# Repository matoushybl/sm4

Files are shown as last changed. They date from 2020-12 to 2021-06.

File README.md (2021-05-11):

# SM4 Stepper motor controller

This repository contains everything related to the SM4 Stepper motor controller project.

The project structure is as follows:
```
.github/ ... workflows for CI, releases, etc.
Hardware/ ... everything related to hardware - KiCAD projects, DS, etc.
Poster/ ... source file for a future poster
Software/ ... the controller and embedded firmware
Thesis/ ... the TeX source code for my Master's Thesis
```

## Authors
* Matous Hybl

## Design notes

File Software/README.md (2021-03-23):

# Software

## Known issues

* the main loop cannot run @ 1 kHz as the readings of the encoder timer are zero, this is likely a software bug. The current workaround is to lower the control frequency to 100 Hz.

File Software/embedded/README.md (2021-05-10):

# `SM4-firmware`

> A firmware for the SM4 dual channel stepper motor controller.

## TODO
 - [ ] Test CANOpen
 - [ ] Implement USB
 - [ ] Implement I2C
 - [ ] Improve architecture and module structure

## Dependencies

#### 1. `flip-link`:

```console
$ cargo install flip-link
```

#### 2. `probe-run`:

``` console
$ cargo install probe-run
```

## Setup

## Support

TODO: Add affiliation with university, rust-embedded, etc

The firmware is based on tooling from the [Knurling] project, [Ferrous Systems]' effort at
improving tooling used to develop for embedded systems.

## License

Licensed under MIT license ([LICENSE-MIT](../LICENSE-MIT) or http://opensource.org/licenses/MIT).

[Knurling]: https://knurling.ferrous-systems.com
[Ferrous Systems]: https://ferrous-systems.com/
[GitHub Sponsors]: https://github.com/sponsors/knurling-rs

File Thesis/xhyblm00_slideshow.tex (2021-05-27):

% Soubory musí být v kódování, které je nastaveno v příkazu \usepackage[...]{inputenc}
% (tento soubor je sdílený s textem práce)

\documentclass[%        Základní nastavení
  %draft,    				  % Testovací překlad
  12pt,       				% Velikost základního písma je 12 bodů
	t,                  % obsah slajdů bude vždy začínat od shora (nebude vertikálně centrovaný)
	aspectratio=1610,   % poměr stran bude 16:10 (všechny projektory v učebnách na Technické 12 Brno),
	                    % další volby jsou 43, 149, 169, 54, 32.
	unicode,						% Záložky a informace budou v kódování unicode
]{beamer}				    	% Dokument třídy 'zpráva', vhodná pro sazbu závěrečných prací s kapitolami
%\usepackage{etex}

\usepackage[utf8]		  % Kódování zdrojových souborů je v UTF-8
	{inputenc}					% Balíček pro nastavení kódování zdrojových souborů
	
\usepackage{graphicx} % Balíček 'graphicx' pro vkládání obrázků
											% Nutné pro vložení logotypů školy a fakulty

\usepackage[          % Balíček 'acronym' pro sazby zkratek a symbolů
	nohyperlinks				% Nebudou tvořeny hypertextové odkazy do seznamu zkratek
]{acronym}						
											% Nutné pro použití prostředí 'acronym' balíčku 'thesis'

%% Balíček hyperref je volán třídou beamer automaticky, proto není třeba následujícího kódu:
%\usepackage[
%	breaklinks=true,		% Hypertextové odkazy mohou obsahovat zalomení řádku
%	hypertexnames=false % Názvy hypertextových odkazů budou tvořeny
%											% nezávisle na názvech TeXu
%]{hyperref}						% Balíček 'hyperref' pro sazbu hypertextových odkazů
%											% Nutné pro použití příkazu 'nastavenipdf' balíčku 'thesis'

\usepackage{cmap} 		% Balíček cmap zajišťuje, že PDF vytvořené `pdflatexem' je
											% plně "prohledávatelné" a "kopírovatelné"

%\usepackage{upgreek}	% Balíček pro sazbu stojatých řeckých písmem
											%% např. stojaté pí: \uppi
											%% např. stojaté mí: \upmu (použitelné třeba v mikrometrech)
											%% pozor, grafická nekompatibilita s fonty typu Computer Modern!

%\usepackage{amsmath} %balíček pro sabu náročnější matematiky

\usepackage{booktabs} % Balíček, který umožňuje v tabulce používat
                      % příkazy \toprule, \midrule, \bottomrule

%%%%%%%%%%%%%%%%%%%%%%%%%%%%%%%%%%%%%%%%%%%%%%%%%%%%%%%%%%%%%%%%%
%%%%%%      Definice informací o dokumentu             %%%%%%%%%%
%%%%%%%%%%%%%%%%%%%%%%%%%%%%%%%%%%%%%%%%%%%%%%%%%%%%%%%%%%%%%%%%%

\input{nastaveni}      % v tomto souboru doplňte údaje o sobě, o názvu práce...

%%%%%%%%%%%%%%%%%%%%%%%%%%%%%%%%%%%%%%%%%%%%%%%%%%%%%%%%%%%%%%%%%%%%%%%%

%%%%%%%%%%%%%%%%%%%%%%%%%%%%%%%%%%%%%%%%%%%%%%%%%%%%%%%%%%%%%%%%%%%%%%%%
%%%%%%     Nastavení polí ve Vlastnostech dokumentu PDF      %%%%%%%%%%%
%%%%%%%%%%%%%%%%%%%%%%%%%%%%%%%%%%%%%%%%%%%%%%%%%%%%%%%%%%%%%%%%%%%%%%%%
%% Při vloženém balíčku 'hyperref' lze použít příkaz '\pdfsettings'
\pdfsettings
%  Nastavení polí je možné provést také ručně příkazem:
%\hypersetup{
%  pdftitle={Název studentské práce},    	% Pole 'Document Title'
%  pdfauthor={Autor studenstké práce},   	% Pole 'Author'
%  pdfsubject={Typ práce}, 						  	% Pole 'Subject'
%  pdfkeywords={Klíčová slova}           	% Pole 'Keywords'
%}
\hypersetup{pdfpagemode=FullScreen}       % otevření rovnou v režimu celé obrazovky
%%%%%%%%%%%%%%%%%%%%%%%%%%%%%%%%%%%%%%%%%%%%%%%%%%%%%%%%%%%%%%%%%%%%%%%

\usetheme{VUT} 				% barvy a rozložení prezentace odpovídající VUT FEKT
% alternativně lze použít jiná berevná témata, ale bez záruky. Například: 
%\usetheme{Darmstadt} \usecolortheme{default2}
\logoheader					% vytvoření zkráceného loga VUT FEKT v hlavičce slajdu, nechte odkomentované

\begin{document}

% v případě zakomentování následujícího se zobrazí v pravém dolním rohu slajdů klikatelné navigační symboly 
\disablenavigationsymbols

% titulní snímek, vysazen bez horních, dolních a postranních lišt (volba plain),
% není tak vysazen ani nadpis snímku
\maketitle

%%%%%%%%%%%%%%%%%%%%%%%%%%%%%%%%%%%%%%%%%%%%%%%%%%%%%%%%%%%%%%%%%%%%%%%
% 1. snímek s cíli (zadaním) práce
\begin{frame} 
	% nadpis snímku
	\frametitle{Cíle práce}
	\begin{itemize}
			\item Nastudovat
			\item Popsat
				\begin{itemize}
					\item nastudované
				\end{itemize}
			\item Implementovat
				\begin{itemize}
					\item nastudované
					\item nové
				\end{itemize}
			\item Porovnat a vyhodnotit
				\begin{itemize}
						\item výsledky
				\end{itemize}
	\end{itemize}
\end{frame}

%%%%%%%%%%%%%
\begin{frame} 
	\frametitle{Klíčové nástroje}

	% prostředí 'alertblock', které slouží pro zdůraznění informace
	\begin{alertblock}{Pro práci je klíčový Eulerův vzorec}
		$$\eul^{\jmag x}=\cos x + \jmag\sin x$$
	\end{alertblock}

	\vspace{4ex}
	Eulerova identita je speciálním případem tohoto vzorce, jestliže dosadíme $x=\uppi$\,:

	% prostředí 'block', které slouží jako informativní
	\begin{block}{Eulerova identita}
		$$\eul^{\jmag \uppi}=\cos \uppi + \jmag\sin \uppi,$$\\
		odkud vyplývá
		$$\eul^{\jmag \uppi}+1=0.$$
	\end{block}
\end{frame} 

%%%%%%%%%%%%%
\begin{frame} 
	\frametitle{Plošný spoj}
	
	\begin{columns}[T] 								% prostředí sloupce s umístěním nahoře
		\begin{column}{0.4\textwidth}		% první sloupec
			Obrázek znázorňuje model:\\[2ex]
			%
			\begin{itemize}
				\item Deska
				\item Součástky
				\item Signály
				\item Napájení
			\end{itemize}
		\end{column}
		%
		\begin{column}{0.6\textwidth}		% druhý sloupec
			\begin{figure}%	
				\centering
				\vspace{1cm}	              % horizontální mezera
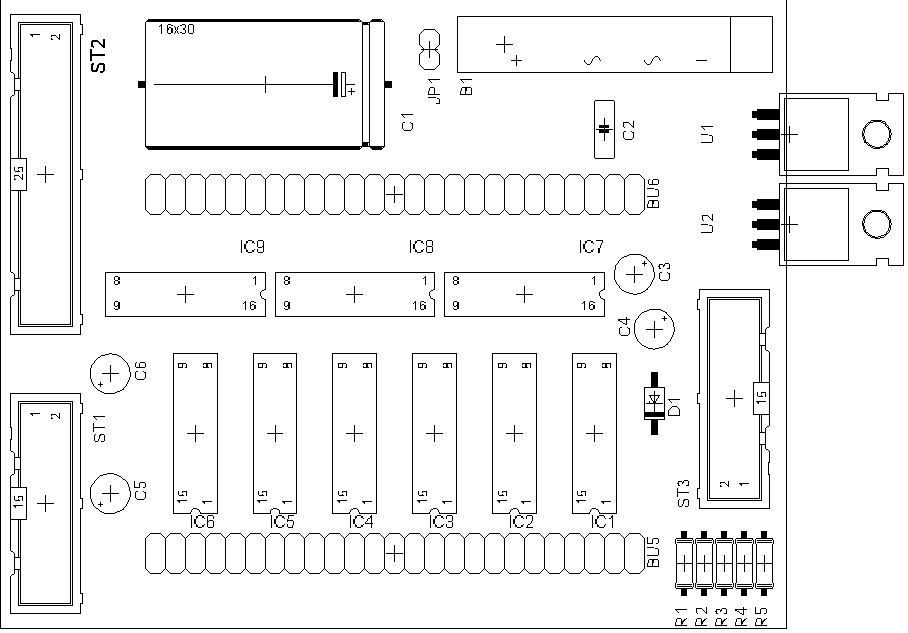
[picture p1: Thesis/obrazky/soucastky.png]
				
				%lze vložit popisek, ale povetšinou je to v prezentaci zbytečné
				%\caption{Popisek obrázku}%
				%\label{obr:ukazka}
			\end{figure}
		\end{column}
	\end{columns}											% ukončení prostředí sloupce
\end{frame}

%%%%%%%%%%%%%
\begin{frame} 
	\frametitle{Výsledky}
	\vspace{1cm}
	\begin{table}[]
		\centering
		\caption{Výsledky měření mobilních sítí}
		\label{tab:tabulka}
			\begin{tabular}{lcc}
				\toprule
					Technologie  & Rychlost stahování [kB/s] & Rychlost nahrávání [kB/s] \\
				\midrule
					GPRS (2,5G)	& 7,2 	& 3,6\\
					UMTS 3G     & 48 		& 48\\
					HSPA (3,5G)	&	1\,706	&	720\\
					LTE (4G) 		& 40\,750 & 10\,750\\
				\bottomrule                                       
			\end{tabular}
	\end{table}
\end{frame}

%%%%%%%%%%%%%
\begin{frame} 
	\frametitle{Závěr}
	\dots
\end{frame}

% podekovani
\begin{frame}[c] 
% bez nadpisu snímku
	\frametitle{\mbox{ }}
	\begin{center}
		{\Huge Děkuji za pozornost!}
	\end{center}
\end{frame}

% otázky oponenta
\frame{
\frametitle{Otázky oponenta}
	\emph{Jaká je souvislost Vašeho vzorce (1.2) s~Maxwellovými rovnicemi v~integrálním tvaru?}\\[2ex]
	%
	Již staří Římané\,\dots
}

\end{document}

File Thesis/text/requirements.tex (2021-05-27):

\section{Requirements}
\label{sec:requirements}
In the book Better Embedded System Software\cite{koopman_better_2010}, the author specifies written requirements as one of the most important parts of documentation for any embedded system.
The author describes requirements as rules specifying everything the system must do, everything the system must not do, and constraints the system must meet.
According to the book, there are three types of requirements - functional requirements, non-functional requirements, and constraints.
An essential property of requirements is that they must be easily verifiable and, if possible, directly measurable.
Also, for future reference, every requirement must have a unique number.

\subsection{Functional Requirements}
\label{subsec:func_req}
Functional requirements describe properties that must be provided by the target system.
These are implemented either by the firmware or the hardware.

The requirements for the stepper-motor controller are specified as follows:

\begin{itemize}
    \item \textbf{FR-01} When no command specifying motor speed is received for a period of time (configurable, e.g., 1~s), the controller shall stop both motors.
    \item \textbf{FR-02} When multiple communication interfaces are connected, the system shall prioritize CAN bus, then I2C. USB has the lowest priority.
    \item \textbf{FR-03} The controller shall set motor current based on the ramping state.
    When the motor is still, low current shall be set; when the motor is accelerating, high current shall be set; when the motor is moving with constant speed, the current shall be set to some medium values.
    These values shall be configurable.
    \item \textbf{FR-04} All relevant values (currents, timings, limits, etc.) shall be configurable via USB or CANOpen SDO protocol.
    \item \textbf{FR-05} The controller shall be able to ramp the speeds using at least trapezoidal ramps, and their parameters shall be configurable.
    \item \textbf{FR-06} The controller shall support control in speed mode as well as position mode.
    \item \textbf{FR-07} The controller shall provide basic electrical safety features - such as fuses and reverse voltage protection.
    \item \textbf{FR-08} The controller shall have an interface allowing to connect external encoders (absolute or incremental) during future development.
\end{itemize}

\subsection{Non-functional Requirements}
\label{subsec:nonfunc_req}
Non-functional requirements are properties that the system must have but are not directly features or functions but rather properties of the system as a whole.

\begin{itemize}
    \item \textbf{NFR-01} The controller shall provide developer-friendly protocol and data formats.
    \item \textbf{NFR-02} The controller shall be programmable without a programmer, ideally using \acs{dfu} (\acl{dfu}).
    \item \textbf{NFR-03} The controller shall be configurable using a program for personal computers.
    \item \textbf{NFR-04} The firmware shall be easily extensible.
    \item \textbf{NFR-05} The firmware shall employ unit testing for \acs{qa} (\acl{qa}).
    \item \textbf{NFR-06} The firmware should utilize software in the loop integration testing for \acs{qa}.
    \item \textbf{NFR-07} The firmware shall be properly documented.
    \item \textbf{NFR-08} The functionality of the controller shall be demonstrated using two distinctive applications.
\end{itemize}

\subsection{Constraints}
\label{subsec:constraints}
Constraints specify limitations on how the system must be built.
They specify, for example, hardware limitations, technologies, protocols, conformance to standards, etc.

\begin{itemize}
    \item \textbf{C-01} The controller shall utilize stepper drivers with silent operation, such as Trinamic StealthChop\texttrademark.
    \item \textbf{C-02} The controller shall be able to drive motors with phase current of up to 2~A RMS.
    \item \textbf{C-03} The controller shall feature CAN bus, I2C bus and USB.
    \item \textbf{C-04} The controller shall utilize two stepper motor drivers.
    \item \textbf{C-05} The controller shall adhere to the CANOpen protocol.
    \item \textbf{C-06} The controller hardware shall be small, ideally smaller than the Raspberry Pi SBC.
    \item \textbf{C-07} The firmware for the controller shall be developed using the Rust programming language.
\end{itemize}

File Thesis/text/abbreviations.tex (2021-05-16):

\cleardoublepage
\chapter*{\listofabbrevname}
\phantomsection
\addcontentsline{toc}{chapter}{\listofabbrevname}

\begin{acronym}[KolikMista]

	\acro{adc}[ADC]{Analog to Digital Converter}
	\acro{ai}[AI]{Artificial Intelligence}
	\acro{api}[API]{Application Programming Interface}
	\acro{arm}[ARM]{Acorn RISC Machine}
	\acro{can}[CAN]{Controlled Area Network}
	\acro{ci}[CI]{Continuous Integration}
	\acro{dc}[DC]{Direct Current}
	\acro{dac}[DAC]{Digital to Analog Converter}
	\acro{dma}[DMA]{Direct Memory Access}
	\acro{dsl}[DSL]{Domain Specific Language}
	\acro{dfu}[DFU]{Device Firmware Update}
	\acro{eeprom}[EEPROM]{Electrically Erasable Programmable Read-Only Memory}
	\acro{emi}[EMI]{ElectroMagnetic Interference}
	\acro{esd}[ESD]{ElectroStatic Discharge}
	\acro{ffi}[FFI]{Foreign Function Interface}
	\acro{fram}[FRAM]{Ferroelectric Random Access Memory}
	\acro{gnd}[GND]{Ground}
	\acro{gpio}[GPIO]{General Purpose Input Output}
	\acro{gui}[GUI]{Graphical User Interface}
	\acro{hal}[HAL]{Hardware Abstraction Layer}
	\acro{ic}[IC]{Integrated Circuit}
	\acro{iic}[I2C]{Inter-Integrated Circuit}
	\acro{ide}[IDE]{Integrated Development Environment}
	\acro{ldo}[LDO]{Low DropOut}
	\acro{led}[LED]{Light Emitting Diode}
	\acro{lidar}[LIDAR]{Light Detection and Ranging}
	\acro{mcu}[MCU]{Microcontroller Unit}
	\acro{no}[NO]{Normally Open}
	\acro{pac}[PAC]{Peripheral Access Crate}
	\acro{pcb}[PCB]{Printed Circuit Board}
	\acro{ptc}[PTC]{Positive Temperature Coefficient}
	\acro{pwm}{PWM}{Pulse Width Modulation}
	\acro{qa}[QA]{Quality Assurance}
	\acro{ram}[RAM]{Random Access Memory}
	\acro{ral}[RAL]{Register Access Layer}
	\acro{risc}[RISC]{Reduced Instruction Set Computer}
	\acro{rms}[RMS]{Root-Mean Square}
	\acro{rps}[RPS]{Revolutions per Second}
	\acro{rtic}[RTIC]{Real-Time Interrupt Driven Concurrency}
	\acro{rtt}[RTT]{Real-Time Transfer}
	\acro{sbc}[SBC]{Single Board Computer}
	\acro{spi}[SPI]{Serial Peripheral Interface}
	\acro{spdt}[SPDT]{Single Pole Double Throw}
	\acro{svd}[SVD]{System View Description}
	\acro{tui}[TUI]{Terminal User Interface}
	\acro{ub}[UB]{Undefined Behavior}
	\acro{usb}[USB]{Universal Serial Bus}

\end{acronym}

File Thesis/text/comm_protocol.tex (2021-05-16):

\section{Communication Protocols}
\label{sec:comm_protocols}
According to the thesis instruction and the requirements \textbf{FR-04}, \textbf{NFR-02}, \textbf{C-03}, \textbf{C-05}, the stepper driver should feature CANOpen and I2C interfaces for control and configuration.
The USB interface shall be used only for configuration.
This section aims to give a brief overview of these communication interfaces and protocols utilized with them.

\subsection{CANOpen}
\label{subsec:canopen}
CANOpen is a set of higher-level protocols based on the CAN bus physical and link layer.
The protocols are designed around the Master-Slave model, where there is a specific device acting as the master which controls the CANOpen network (e.g., synchronization) and up to 127 slave devices-nodes.
Every device in a CANOpen network is assigned a unique ID.
Within the CANOpen protocols, the CAN frame sent to the device either targets a specific device or all of them.
The frames that target specific devices contain the identifier of the frame (e.g., PDO CAN ID) bit-or with the device ID.
The CANOpen protocols provide standardized communication objects (COBs) with specific identifiers (IDs) for time critical processes, communication and network management\cite{can_in_automation_can_2021}.
The most critical parts CANOpen protocol is the SYNC protocol, the PDO protocol, the SDO protocol, and the NMT protocol.
Other protocols are the EMCY protocol, TimeStamp protocol, and LSS protocol.

\subsection{Object Dictionary}
\label{subsec:object_dictionary}
In a CANOpen device, the Object Dictionary contains the global shared state of a device.
This means that the software responsible for communicating over CANOpen protocols sends out the data available in the Object Dictionary and, in turn, writes to it the received data.
Apart from being a data storage for the communication interface, the Object Dictionary serves as a data source for the algorithms and systems running on the device itself.
There are two numbers used to access the values in the Object Dictionary - first, the Index - a 16-bit unsigned value, and the SubIndex - an 8-bit unsigned value.
Some of the Index ranges are reserved by the CANOpen specification for predefined parameters such as communication settings, while other Index ranges contain application-specific parameters\cite{can_in_automation_can_2021}.

\subsubsection{SYNC protocol}
The SYNC protocol is responsible for synchronizing the communication on the bus.
It initiates the transfer by sending a CAN frame with the identifier \textbf{0x80}, after which every device on the bus sends/receives synchronous data objects, such as PDOs (Process Data Units).
The CAN frame can also contain a single byte containing a SYNC number that can be utilized to conditionally send synchronous data or for more granular synchronization\cite{can_in_automation_can_2021}.
SYNC message is generally sent periodically.

\subsubsection{PDO protocol}
Process Data Objects (PDOs) are used for broadcasting high-priority status and control information\cite{can_in_automation_can_2021}.
Each PDO consists of a single CAN bus frame and can contain up to 8 bytes of data.
The contents of the PDO can be set in some devices according to the specific application needs using a technique called PDO mapping, where PDO data are mapped to Object Dictionary fields.
There are three mechanisms used to transmit PDOs - asynchronous PDOs can be sent upon an event trigger in the device.
Asynchronous PDOs can also be remotely requested using the RTR bit in the CAN frame.
Synchronous PDOs are broadcast as a reaction to the SYNC protocol.
There are two types of PDOs - RxPDOs and TxPDOs.
The RxPDOs are the PDOs that are received by the target device, while the TxPDOs are the PDOs that are transmitted by the target device.
There are four available RxPDOs and four available TxPDOs each PDO has a CAN ID assigned, as can be seen in the Table~\ref{tab:pdo}.

\begin{table}[H]
    \centering
    \begin{tabular}{ |c|c|c| }
        \hline
        PDO & RxPDO CAN ID & TxPDO CAN ID \\
        \hline
        \hline
        PDO1 & 0x200 & 0x180 \\
        \hline
        PDO2 & 0x300 & 0x280 \\
        \hline
        PDO3 & 0x400 & 0x380 \\
        \hline
        PDO4 & 0x500 & 0x480 \\
        \hline
    \end{tabular}
    \caption{RxPDO and TxPDO CAN IDs\cite{noauthor_canopen_2021}}
    \label{tab:pdo}
\end{table}

\subsubsection{SDO protocol}
The SDO (Service Data Object) protocol is used to directly read or write entries of the device's object dictionary.
This protocol utilizes the client-server model, where the device with the target Object Dictionary is the server, and the other device is the client.
One SDO consists of two CAN frames with different IDs that represent the transaction.
Given there are two CAN frames, the protocol is confirmed\cite{can_in_automation_can_2021}.

There are three variants of the SDO protocol - expedited transfer, normal (segmented) transfer, and block transfer.
The expedited transfer can be utilized when the target data has a length of 4 bytes or less.
To transfer data with greater length the segmented, or the block transfers may be used, where the block transfer shall have a slightly lower protocol overhead\cite{noauthor_canopen_2021}.

\subsubsection{NMT protocol}
NMT (Network Management) protocol is a protocol implemented by all the slave devices in the network.
It consists of a finite state machine that describes the device's state with relation to the bus and the rest of the system.
The states are \textbf{Initialization}, \textbf{Preoperational}, \textbf{Operational} and \textbf{Stopped}.
After the device starts, it shall automatically enter the \textbf{Initialization} state.
Using an NMT command CAN frame, the device goes to the next state, in this case, \textbf{Preoperational}.
The state themselves have a certain meaning for the behavior of the device.
For example motor movement must be disabled until the device enters the \textbf{Operational} state.

While the master controls the slave devices by commanding them to go to a certain state, the slave devices use the NMT Heartbeat protocol to periodically notify the master (and other devices) of their current state.
Devices can be configured to, for example, stop movement if another slave device or master stops sending these Heartbeat messages.

\subsubsection{CAN bus}
The Controlled Area Network is a bus most commonly used in automotive for connecting ECUs (Electronic Control Units).
The bus was developed by Bosch and codified into the ISO11898-1 standard.
CAN bus utilizes a single differential pair making simplifying the wiring of a complex system consisting of many ECUs\cite{st_michael_introduction_2019}.

On the physical layer, the bus has two states - recessive and dominant, where recessive means that the differential voltage between the CANH and CANL signals is less than a minimum threshold voltage.
In contrast, the dominant state means that the differential voltage is higher than the minimal threshold voltage\cite{st_michael_introduction_2019}.
The dominant state is achieved by sending a logical 0 through the network, while the recessive state is achieved by sending logical 1.
CAN bus utilizes the CSMA/CD media access control protocol, which allows for collision detection and potential retransmission of CAN frames.
For collision detection, it is vital that the dominant state overrides a recessive one.

There are two types of frames transmitted on the bus - standard frames and extended frames.
These frames differ in the identifier length, where the extended frame allows for 29-bit long identifier in contrast to the standard frame, which allows for only 11-bits.
Identifier length is selected on a per-frame basis using the IDE bit in the frame.
Each CAN frame may contain up to 8 bytes of data, and the data length is controlled by the four DLC bits in the frame.
The structure of a CAN frame can be seen in the Figure~\ref{fig:can_frame}.

\begin{figure}[H]
    \centering
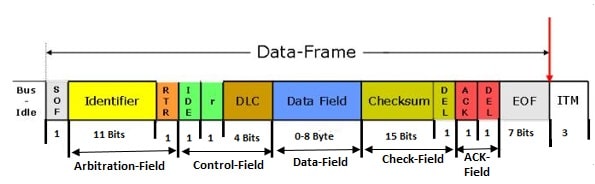
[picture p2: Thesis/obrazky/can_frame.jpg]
    
    \caption{CAN bus frame with standard identifier~\cite{piembsystech_can_nodate}.}
    \label{fig:can_frame}
\end{figure}

An important bit for CANOpen is the RTR bit which stands for Remote Transmission Request, when this bit is recessive, there are no data in the frame, and the frame asks the remote device for data.
As can be seen in the Figure, the identifier and the RTR field are part of an Arbitration field, these bytes are used in the shared medium collision detection and control, and thanks to this field, frames with lower ID have a higher priority in the transmission.

\subsection{I\textsuperscript{2}C}
\label{subsec:i2c}
I\textsuperscript{2}C (Inter-Integrated Circuit) bus is a bus, that allows connecting multiple peripheral (slave) ICs to a controller (master) IC (multi-master mode is also supported)\cite{sfuptownmaker_i2c_2021}.
Hardware-wise the bus utilizes two pins in open collector configuration, which means that the high-level voltage needs to be provided externally using a pull-up resistor.
The resistance value of the pull-up resistor affects the bus performance and can be fine-tuned to compensate for the parasitic capacity for the wiring.
The open-collector configuration also means that when idle, the bus is pulled up to the defined voltage level, and when the device wants to transmit data, it can only pull the signal down.
The I\textsuperscript{2}C bus consists of two signals - the data signal (SDA) and the clock signal (SCL).

The I\textsuperscript{2}C transaction begins when the controller sends a START condition on the bus, the START condition is followed by the peripheral device address, and a direction bit determining whether the controller wants to write or read from the peripheral device\cite{sfuptownmaker_i2c_2021}.
Then based on the direction bit, the controller either receives data or sends them.
The peripheral has a mechanism of stopping the clock signal in the event the peripheral is not fast enough to produce data, which is done by pulling the clock signal low and then releasing it when the data are available.
When the data is transferred, the controller finalizes the transfer by sending the STOP condition.

When interfacing with various peripherals, the read and write transactions are combined\cite{valdez_understanding_2015}.
The controller first sends the peripheral address (with direction bit set to write) followed by the register it wants to access, the register is ACKed, and now the controller either sends the data to be written or issues a Repeated START, transmits peripheral address with direction bits set to read and awaits data from the peripheral.
Writing to a peripheral using this approach can be seen in the Figure~\ref{fig:i2c_w} and reading data can be seen in the Figure~\ref{fig:i2c_r}.

\begin{figure}[H]
    \centering
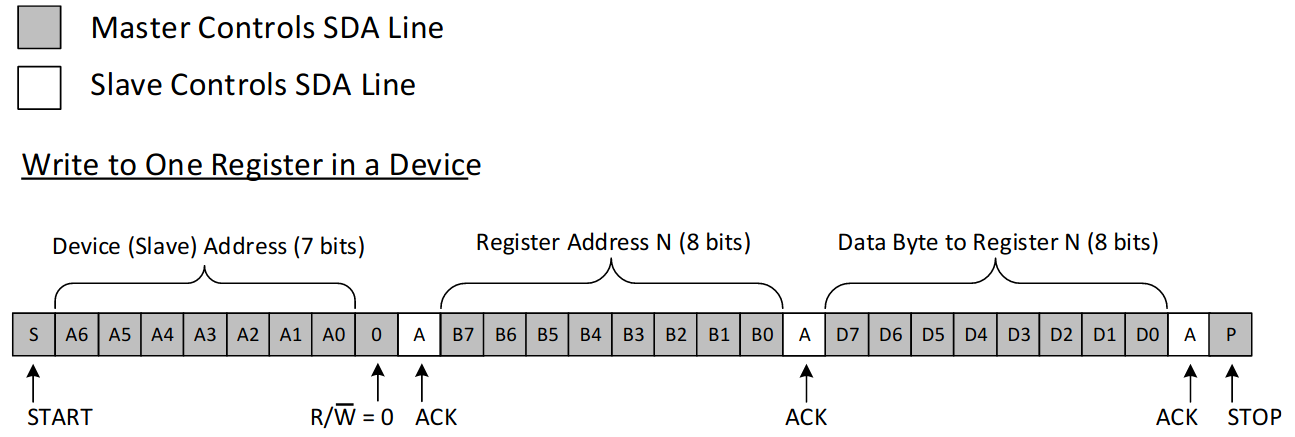
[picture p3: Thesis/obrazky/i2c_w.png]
    
    \caption{Writing to a register of an I\textsuperscript{2}C peripheral IC~\cite{valdez_understanding_2015}.}
    \label{fig:i2c_w}
\end{figure}

\begin{figure}[H]
    \centering
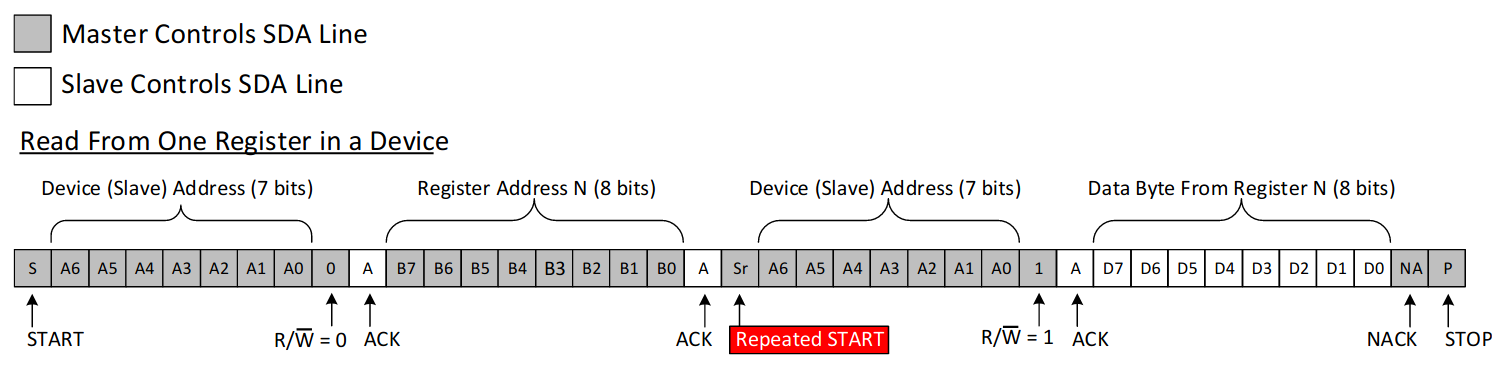
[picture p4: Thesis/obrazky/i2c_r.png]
    
    \caption{Reading a register of an I\textsuperscript{2}C peripheral IC~\cite{valdez_understanding_2015}.}
    \label{fig:i2c_r}
\end{figure}

\subsection{Universal Serial Bus}
\label{subsec:usb}
USB (Universal Serial Bus) utilizes a differential pair (or multiple) for data transfer.
Nowadays, USB devices are ubiquitous and perform a variety of different functions, and according to these functions are separated into classes (Mass Storage, HID (Human Interface Devices), etc.).
Through time, there were four major revisions of the USB standard as can be seen in the Table~\ref{tab:usb}.

\begin{table}[H]
    \centering
    \begin{tabular}{ |c|c|c| }
        \hline
        Version & Max. Data Rate & Code Name \\
        \hline
        \hline
        1.0 & 1.5 Mbit/s & Low Speed \\
        \hline
         & 12 Mbit/s & Full Speed \\
        \hline
        2.0 & 480 Mbit/s & HighSpeed \\
        \hline
        3.0 & 5 Gbit/s & SuperSpeed \\
        \hline
        3.1 gen 2 & 10 Gbit/s & SuperSpeed+ \\
        \hline
        3.2 & 20 Gbit/s & SuperSpeed+ USB dual-line \\
        \hline
        4.0 & 40 Gbit/s &  \\
        \hline
    \end{tabular}
    \caption{USB versions and data rates~\cite{noauthor_usb_2021}}
    \label{tab:usb}
\end{table}

USB is nowadays everywhere, with different supported transfer data rates, different utilization of connectors, etc.
With such diverse use cases and devices, the whole USB ecosystem is increasingly more difficult to orient within.
For our use case, we'll be utilizing the USB controller present on the MCU, which is a USB 2.0 OTG (On The Go) Full Speed device\cite{stmicro_an4879_2018}, but to support better compatibility and mechanical properties, we'll be using the USB-C receptacle with both differential data lanes interconnected.

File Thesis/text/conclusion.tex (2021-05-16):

\chapter*{Conclusion, Discussion and Future work}
\phantomsection
\addcontentsline{toc}{chapter}{Conclusion, Discussion and Future work}
In this thesis, we described the development of a dual-channel stepper motor controller we named SM4.
We developed both the hardware and software.
As for the hardware development, we utilized the STM32F405 MCU and Trinamic stepper motor driver ICs as the basis of the design.
As for PCB design, we utilized a 4-layer PCB to decrease the development time, and we utilized the JLCPCB's manufacturing service alongside the PCB assembly service.
Two revisions of the PCB were designed and manufactured, two of each revision PCBs were assembled.
Even though the second revision of the PCB is more advanced than the first one, there is still plenty of room for improvements, which we came across during the development.
The schematic and PCBs were designed in the KiCAD EDA suite, which proved useful, given the fact that KiCAD has a large footprint and symbol library.

As for the development of the software, we utilized the Rust programming language for both the bare-metal firmware and the control application.
Unfortunately, the firmware, as of now, supports only the first revision of the hardware.
Developing the firmware in Rust proved useful, as there is great support for developing on bare-metal, given there is a large community for developing device drivers, HALs, and tooling.
During the development, we utilized many of the language's features, especially when developing abstractions over the hardware where we utilized traits and generics.
We believe that given the developed abstractions the firmware can be easily extended and improved.

We believe that the tooling that currently exists surpasses the tooling available for other languages and ecosystems.
The language's features provide memory and data race safety for embedded systems while not impeding the code size or performance.
Given our experience with developing embedded firmware for this project and several other ones described earlier, we firmly believe that the Rust programming language is the right way forward as it brings features never deemed possible for embedded systems development.

Apart from the firmware, we also developed a simple control application for personal computers that is now capable of only controlling the stepper motor controller but not of configuring it.
The control application is now able to control the controller's axis in both velocity and position modes.

Even though there is still a lot of work to be done, we believe that the controller is currently usable and be deployed, for example, to be part of the BPC-PRP course.

\section{Future work}
\label{sec:fut_job}
We are hoping to continue working on the stepper motor controller in the future.
We would like to greatly extend and improve both the hardware and software (and both the firmware and the control application).
Some of the requirements were not completely fulfilled, and we are aiming to revisit them.
A big part of the future development will be finishing the documentation and automated testing.
Extending the firmware with support for the second hardware revision will be a priority since the new stepper motor controller IC is much more powerful than the one in the first revision.
We are also planning to try integrating real hardware encoders to try out the suitability of the abstractions and the ability to control the motors with proper feedback.
We will also aim for full conformance with the CANOpen standard to allow for seamless integration with other systems.
We are also looking into continuing the development using Rust programming language for embedded systems, either by developing more projects using it or contributing to the existing ecosystem by developing the tooling and libraries.

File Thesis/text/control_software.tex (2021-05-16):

\section{Development of the Control Application}
\label{sec:control_sw}
Control software was developed to ease testing of the stepper motor controller functionality.
The control software was also developed in the Rust programming language, utilizing a crate for \acs{tui} (\acl{tui}) and the shared components library from the bare-metal firmware.
Initially, we aimed to develop a fully-featured \acs{gui} (\acl{gui}) based on the GTK framework, but this work hasn't left the prototyping stage as the learning curve for integrating GTK is quite steep.
In the Figure~\ref{fig:tui} we can see the control application, and in the Figure~\ref{fig:gui}, there is a screenshot of the proposed \acs{gui} developed with the GTK framework.

\begin{figure}[H]
    \centering
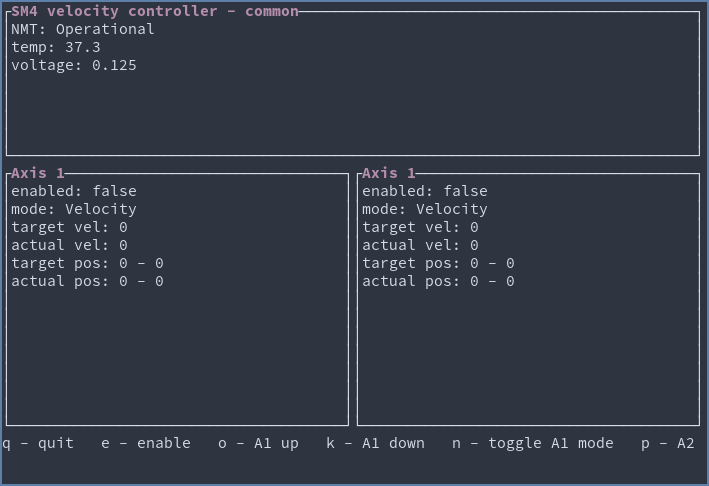
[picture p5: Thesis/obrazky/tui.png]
    
    \caption{The TUI control application.}
    \label{fig:tui}
\end{figure}

\begin{figure}[H]
    \centering
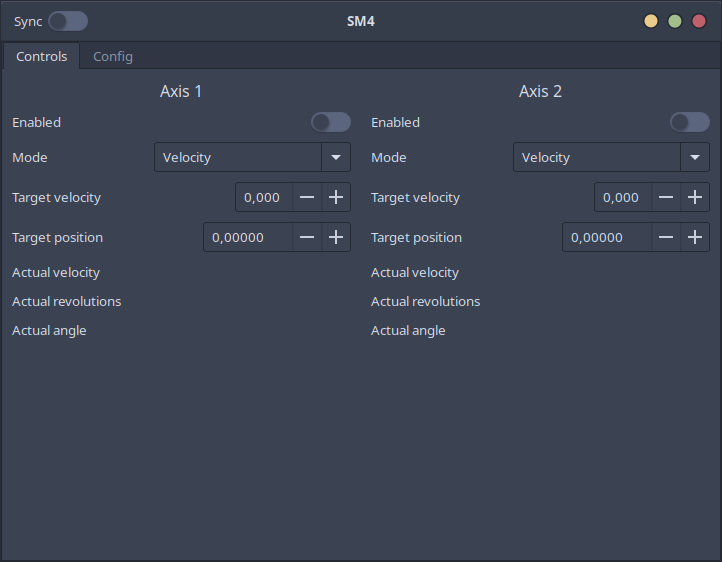
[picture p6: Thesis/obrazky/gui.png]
    
    \caption{The proposed GUI control application.}
    \label{fig:gui}
\end{figure}

For communication with the stepper motor controller, the control application utilizes CANOpen protocol.
It periodically transmits \textbf{SYNC} frames and displays the contents of the received \textbf{PDO}s.
On various keypresses, it changes the values of the control variables (such as axis target velocity and target position) and sends them to the controller.
This way, it can be easily tested whether the controller works as expected.

In the future, apart from developing a proper \acs{gui} for the control application, we want to add support for all the remaining communication interfaces and configuring all the parameters of the stepper motor controller.

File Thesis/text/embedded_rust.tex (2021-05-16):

\section{Embedded Rust}
\label{sec:embedded_rust}
Embedded Rust is enabled by two crate-level attributes - \textbf{no\_main} and \textbf{no\_std}.
The \textbf{no\_main} attribute indicates that the compiler will not emit a main symbol automatically but instead expects the crate to define it itself\cite{noauthor_crates_2021}.
The \textbf{no\_std} attribute, on the other hand, indicates that the final program will not link against the std crate (containing functions usable with operating systems and heap allocation) but instead will link against the core crate, which contains only those parts of the standard library that are platform agnostic.
The core crate includes, for example, language primitives, such as floats, slices, and support for atomic instructions.
Rust program with the \textbf{no\_std} attribute and therefore linking to core library can be used for bootstrapping code like bootloaders, firmware or kernels\cite{rust_embedded_devices_wg_introduction_2021}.

Using the \textbf{no\_main} requires the programmer to write their own program entry point and some other functions, such as the reset handler and panic handlers.
An example of such low-level project bring-up can be seen in~\cite{munns_zero_2019}.
Developing such low-level program can be quite hard and is usually platform-dependent.
Thankfully, for the supported \acs{mcu}s, this is already pre-implemented by processor low-level access crates and their startup and runtime crates.

We've mentioned that developing \textbf{no\_std} does not by default use heap allocation.
Heap allocation can however be added to \textbf{no\_std} programs by implementing a custom allocator such as the \textbf{alloc-cortex-m} crate\cite{rust_embedded_devices_wg_rust-embeddedalloc-cortex-m_2021}, that implements an allocator for Cortex-M \acs{mcu}s.
Using heap allocation, it is possible to use structures like \textbf{Vec} and \textbf{Box<T>}\cite{noauthor_alloc_nodate}.
It also seems to be possible to run a subset of the Rust std library directly on a \acs{mcu}\cite{hutt_using_nodate}, but this approach is still in the early stages of development.

\subsection{Platform Support}
\label{subsec:platform_support}
To compile Rust programs for specific \acs{mcu} core, it is required that target support for it is first available in LLVM and second that a target for it exists within the Rust ecosystem (existence of a target means, that the rust compiler and other tools and can be built for the target).
Rust targets are also split into tiers differentiating different amounts of support from the Rust teams, where the majority of the embedded targets are in Tier 2, meaning that the compilation of the tools must succeed for every change in the compiler.
Still, automated tests of the resulting builds are not guaranteed to run.
As of now, there is support for different \acs{arm} architectures, such as aarch64, armv7, armv6, thumbv8, thumbv7, thumbv6 (both with hardware FPU and without) etc\cite{noauthor_platform_nodate}.
Apart from \acs{arm} support, there is also support for \acs{risc}-V targets, Tier 3 also contains support for AVR\cite{noauthor_platform_nodate, rahul_how_nodate} and MSP430.
There also seems to be some effort into bringing the Xtensa architecture (ESP8266 and ESP32)\cite{mabin_mabezdevxtensa-rust-quickstart_2021} into the Rust ecosystem as the work of supporting the architecture in LLVM seems to be done.

\subsection{Embedded Working Group}
\label{subsec:embedded_wg}
Embedded Rust is one of the official goals of the Rust Language project, and the development of Rust for embedded devices is governed by the Embedded Devices Working Group\cite{noauthor_embedded_nodate}.
Apart from target maintenance, the working group is directly responsible for creating and maintaining documentation - such as the Embedded Rust book\cite{rust_embedded_devices_wg_introduction_2021}, the Discovery book\cite{rust_embedded_devices_wg_introduction_nodate} and the Embedonomicon book\cite{rust_embedded_devices_wg_preface_nodate} and is also responsible for developing several of the critical tools and libraries - such as \textbf{svd2rust}, \textbf{embedded-hal} or \textbf{embedded-dma}.

The working group also governs the work on low level \acs{mcu} core access crates and minimal runtimes for these cores such as the \textbf{cortex-m} and \textbf{cortex-m-rt} or \textbf{risc-v} and \textbf{riscv-rt}.

\subsection{Register Access}
\label{subsec:register_access}
Peripheral and core register access is one of the most vital operations on embedded systems.
Generally, in C/C++, this is done either by operating on a pointer to an integer value or by modifying a struct that contains the configuration.
In embedded Rust, there are two approaches to this problem.

The first approach is the \textbf{svd2rust}\cite{rust_embedded_devices_wg_rust-embeddedsvd2rust_2021} tool.
This tool uses the manufacturer-provided \acs{svd} files that describe registers and their bits and converts them into a Rust \acs{api}.
There are several advantages to this approach - no code needs to be written manually, the resulting register access is compile-time safe, allows for named bit settings instead of non-descriptive setting to logical one or zero, and when there is ambiguity, for example, in integer size, it enforces adding the unsafe keyword, marking that the code should be thoroughly reviewed.
An example of setting register values using this approach can be seen in the following Listing~\ref{lst:svd2rust}, where we are configuring channel of an advanced control timer.
The disadvantage of this approach is that given the size of the \acs{svd} files, and the number of \acs{mcu}s, the compilation is quite long, and given the resulting \acs{api} complexity, the contemporary \acs{ide}s have problems resolving it for automatic code completion.
This approach is prevalent with the majority of the \acs{pac}s (\acl{pac}s), for example with the \textbf{stm32-rs} crate\cite{noauthor_stm32-rsstm32-rs_2021}.

\newpage
\begin{lstlisting}[caption={Using svd2rust generated API for register access.},label=lst:svd2rust]
timer.ccmr2_output().modify(|_, w| {
    w.cc4s()
        .output() // channel 4 as output
        .oc4fe()
        .set_bit() // enable fast output
        .oc4pe()
        .set_bit() // enable preloading
        .oc4m()
        .toggle() // set mode (3bit wide register part)
});
\end{lstlisting}

Another and more lightweight approach is utilization of RAL (Register Access Layer) crates, for example the \textbf{stm32ral}\cite{greig_adamgreigstm32ral_2021}.
This approach also parsed the \acs{svd} files, but generates simpler structures, and \acs{api}.
An example of using this approach can be seen in the Listing~\ref{lst:ral}.
\begin{lstlisting}[caption={Using RAL API for register access\cite{greig_adamgreigstm32ral_2021}.},label=lst:ral]
modify_reg!(rcc, rcc, AHB1ENR, GPIOAEN: Enabled);
modify_reg!(gpio, gpioa, MODER, MODER1: Input, MODER2: Output, MODER3: Input);
\end{lstlisting}

\subsection{embedded\textendash hal}
\label{subsec:embedded_hal}
The \textbf{embedded-hal} project\cite{rust_embedded_devices_wg_rust-embeddedembedded-hal_2021} is one of the projects developed by the Embedded Devices Working Group.
Its aim is to provide a \acs{hal} (\acl{hal}) abstract enough that device drivers using it may be shared not only between different \acs{mcu}s but also different platforms (\acs{mcu} and Embedded Linux).
This is achieved by utilizing traits described earlier in the Section~\ref{subsec:traits}.
An example of such device driver developed using the traits available in the \textbf{embedded-hal} can be seen in the Listing~\ref{lst:hal_usage}\cite{rust_embedded_devices_wg_rust-embeddedembedded-hal_2021}.
As can be seen in the Listing, the driver will work with any type that implements the \textbf{WriteRead} trait.
Currently, the \textbf{embedded-hal} defines traits for common embedded functionality (such as \acs{gpio}, \acs{adc}) and buses (I\textsuperscript{2}C, \acs{spi}), but only their blocking variants.

\newpage
\begin{lstlisting}[caption={Example of an device driver utilizing embedded\textendash hal traits.},label=lst:hal_usage]
use embedded_hal::blocking::i2c::{TenBitAddress, WriteRead};
const ADDR: u16  = 0x158;
const TEMP_REGISTER: u8 = 0x1;
pub struct TemperatureSensorDriver<I2C> {
    i2c: I2C,
}
impl<I2C, E> TemperatureSensorDriver<I2C>
where
    I2C: WriteRead<TenBitAddress, Error = E>,
{
    pub fn read_temperature(&mut self) -> Result<u8, E> {
        let mut temp = [0];
        self.i2c.write_read(
                ADDR,
                &[TEMP_REGISTER],
                &mut temp
            )
            .and(Ok(temp[0]))
    }
}
\end{lstlisting}

The traits from the \textbf{embedded-hal} are implemented by device \acs{hal}s, such as the \textbf{stm32f4xx-hal}\cite{noauthor_stm32-rsstm32f4xx-hal_2021}, which implements the provided traits for the peripherals of the STM32F4xx \acs{mcu}s.

A crate similar to the \textbf{embedded-hal} is the \textbf{embedded-dma} defining traits for unified \acs{dma} access, so that development of unified device drivers utilizing \acs{dma} is possible.
DMA itself is not that easy problem when aiming for Rust's memory safety\cite{aparicio_memory_nodate}, but a lot of work has been done on its support and perfecting it for safety.

\subsection{Mutable Shared State}
\label{subsec:mut_shared_state}
The Rust programming considers mutable static variables unsafe as they may cause data races in concurrency\cite{noauthor_static_nodate}.
This approach is valid but causes ergonomics problems with embedded programs where storing data in static variables is used for interchanging data between interrupts and blocking code.
In order to write correct, data race free code, the shared state needs to be at least wrapped in a mutex that will synchronize access to the shared resource.
This, however is not enough as the borrow checker will object with invalid access to a shared resource.
Also, when using mutex on embedded systems, the block holding the lock need to be wrapped in a critical section.
Otherwise, the lock could never be freed.
The situation gets more complicated with different interrupt priorities.
An overview of ways of solving this problem can be found in an excellent blog post by one of the members of the Embedded Devices Working group here\cite{egger_look_nodate}.

We decided to use the \acs{rtic} (\acl{rtic}) framework\cite{noauthor_preface_nodate} as a solution to this problem as according to us, the approach is very well thought out.
The framework aims to solve the problem by providing a \acs{dsl} (\acl{dsl}) based on Rust's procedural macros for concurrency on embedded systems.
In short, the \acs{rtic} framework lets the user define shared resources and allows different tasks (either software tasks or interrupt triggered ones) to access those resources in a safe way, removing boilerplate code needed for shared resource handling.
Imagine that there are two interrupt triggered tasks with different priorities wanting to access a shared resource.
The high-priority task can easily access the resource without the need for any explicit locking as it has the privilege to do so, given its priority.
On the other hand, the lower priority task needs to perform locking in order to access the shared resource to avoid the resource being accessed temporarily by the higher resource task, which could lead to a data race.
This behavior is compile-time enforced and checked, bringing another level of safety and security to embedded systems.
Apart from providing safe access to shared resources, this framework also contains a simple scheduler for timed tasks.
Thanks to these features, this framework is nowadays the base of many embedded systems developed in Rust.

\subsection{async/await}
\label{subsec:async}
Async/await is a concurrency model utilizing cooperative tasks.
Cooperative tasks are tasks that yield control back to the scheduler at determined points\cite{aparicio_concurrency_nodate}, and these points are when task switching occurs.
Tasks can yield, for example, to wait for a blocking operation.

This concurrency model may prove extremely useful for embedded systems as it allows for concurrent code to be written in an imperative way, which increases code readability.
Imagine a device driver task that resumes its operation when new data is received and doesn't use any blocking waits.
The code can be read as a sequence of operations instead of, for example, a state machine.

Async/await in the Rust programming language builds upon the \textbf{Future} trait.
A future can be polled, and polling results in reporting whether the \textbf{Future} can resume executing or not.
An executor takes care of periodically (or as a reaction to an event) polling \textbf{Futures} and resumes their execution if needed.
Given the design of async/await, this can be easily used in a \textbf{no\_std} environment, even on low computing power devices, such as the Atmel AVR\cite{schattinger_asyncawait_2020}.
As of now, there are several async runtimes for embedded systems, the most advanced one being \textbf{embassy}, the downside being that it currently requires nightly Rust to build.

An example of utilizing async/await for timed tasks, and \textbf{embassy} can be seen in the Listing~\ref{lst:embassy}

\begin{lstlisting}[caption={Timed tasks using async/await and embassy\cite{noauthor_embassy-rsembassy_2021}.},label=lst:embassy]
#[embassy::task]
async fn run1() {
    loop {
        info!("BIG INFREQUENT TICK");
        Timer::after(Duration::from_ticks(64000)).await;
    }
}
#[embassy::task]
async fn run2() {
    loop {
        info!("tick");
        Timer::after(Duration::from_ticks(13000)).await;
    }
}
#[embassy::main]
async fn main(spawner: Spawner) {
    unwrap!(spawner.spawn(run1()));
    unwrap!(spawner.spawn(run2()));
}
\end{lstlisting}

\subsection{Ecosystem}
\label{subsec:ecosystem}
The Embedded Rust ecosystem is nowadays very vast.
Apart from the Embedded Devices Working Group, there are many smaller organizations governing development for specific platforms or projects.
There are organizations and groups developing crates for \acs{mcu} support (STM32, RISC-V, AVR, RP2040, iMXrt, SAMD, etc.), universal device drivers (using the embedded-hal described earlier), and much more.
The ecosystem also consists of tooling and documentation, which is also under active development, with some tools surpassing traditional tools for embedded development.
More importantly, given Rust's focus on performance and security, eliminating most common bugs, the developers are able to work on the "harder" problems in embedded - for example, drivers for USB\cite{noauthor_stm32-rsstm32-usbd_2021} or Ethernet\cite{noauthor_stm32-rsstm32-eth_2021}.

\subsection{C/C++ Interoperability}
\label{subsec:ccpp_interop}
Thanks to Rust's \acs{ffi} (\acl{ffi}), it is possible to combine code written in C and Rust, even both ways\cite{rust_embedded_devices_wg_interoperability_nodate}.
For example, it is possible to utilize Rust's serialization and deserialization crates in an existing Zephyr project\cite{wolff_embedding_nodate}.
This is especially useful for bringing Rust into the existing embedded codebase, but also for integrating existing the C/C++ codebase into new Rust project.

\subsection{Tooling}
\label{subsec:tooling}
We've already discussed some of the Rust Embedded Tooling, such as the \textbf{svd2rust} in previous sections, but there are more tools at hand helping with the development cycle.
In general, in C/C++ embedded projects, the firmware is flashed via a combination of OpenOCD and GDB.
That used to be the case with Embedded Rust too before the \textbf{probe-rs} project was developed.
The project aims to provide "A debugging toolset and library for debugging embedded ARM and RISC-V targets on a separate host"\cite{probe_rs_project_probe-rsprobe-rs_2021}, this is achieved by developing a library for various probes (ST-Link, J-Link) handling the low-level communication with the target \acs{mcu}s and then building tools upon that library, that allow for flashing and debugging the target \acs{mcu}s.
Those tools are called \textbf{cargo-flash}\cite{probe_rs_project_probe-rscargo-flash_2021}, enabling just flashing, and the \textbf{cargo-embed}\cite{probe_rs_project_probe-rscargo-embed_2021}, enabling flashing, debugging and logging.
The \textbf{probe-rs} project is the project that implements Segger \acs{rtt} (\acl{rtt}) for seamless and fast data transport between the host and the target \acs{mcu} that can be utilized for fast logging.

Thanks to \textbf{probe-rs} architecture, other tools can utilize its algorithms for accessing probes and the target \textbf{mcu}s.
That is what happened with the Knurling project - an initiative to provide modern tooling for embedded development.
At the moment, there are four crucial tools developed by the Knurling project - \textbf{probe-run}, \textbf{defmt}, \textbf{defmt-test} and \textbf{flip-link}.

\subsubsection{defmt}
\textbf{defmt} stands for deferred formatting\cite{knurling_project_knurling-rsdefmt_2021}, which means that the data coming from the \acs{mcu} is formatted when it is received by the host.
This is utilized for logging data from the \acs{mcu}.
The tool strips all strings from the firmware binary and replaces them with their identifier.
Instead of transferring the whole strings, only their identifiers and optional arguments (such as values of variables) are transferred, saving time and resources, making the logging extremely efficient.
This logging technique relies on the fast RTT transfer from \textbf{probe-rs} described earlier.
The end result is a logging interface that is fast and efficient enough to debug extremely fast and timing-sensitive interfaces, such as \acs{usb}.

\subsubsection{probe\textendash run}
\textbf{probe-run} is a runner for Rust programs\cite{knurling_project_knurling-rsprobe-run_2021}, that automatically flashes the firmware binary when \textbf{cargo run} is run and opens a terminal which prints \textbf{defmt} encoded messages transferred over \acs{rtt}.
Another feature is that it can print stack backtraces when the firmware encounters an exception or on a breakpoint.

As of now, the runner doesn't support debugging via GDB, but there have been some developments recently about simultaneous defmt logging and debugging with GDB that stated that GDB support should be possible in the near future\cite{aparicio_using_nodate}.

\subsubsection{defmt\textendash test}
\label{subsubsec:defmttest}
\textbf{defmt-test} is a component of the \textbf{defmt} tool, that can be used for running integration and unit tests directly on the target \acs{mcu}.
We believe that this brings new possibilities for reliability in embedded systems and software/hardware-in-the-loop testing.
An example of such test can be seen in the Listing~\ref{lst:defmttest}\cite{knurling_project_knurling-rsdefmt_2021}.

\newpage
\begin{lstlisting}[caption={Integration test written using defmt\textendash test.},label=lst:defmttest]
struct State {
    scd30: Scd30<Twim<TWIM0>>,
}
#[defmt_test::tests]
mod tests {
    use super::State;
    #[init]
    fn setup() -> State {
        // initialize the hardware (ommited)

        let scd30 = scd30::Scd30::init(i2c);
        State { scd30 }
    }
    #[test]
    fn confirm_firmware_id(state: &mut State) {
        const EXPECTED: [u8; 2] = [3, 66];
        let firmware_id = state.scd30.get_firmware_version().unwrap();
        assert_eq!(EXPECTED, firmware_id);
    }
}
\end{lstlisting}

\subsubsection{flip\textendash link}
The last Knurling tool is \textbf{flip-link}, which is a linker that adds zero-cost stack overflow protection\cite{knurling_project_knurling-rsflip-link_2021}.
The stack overflow protection works by smartly changing the order of \textbf{.stack} and \textbf{.bss+.data} segments of \acs{ram} in a way that when the stack overflows, it doesn't interfere with static variables but instead triggers a hardware exception and doesn't produce corrupted memory.
The change in the memory layout can be seen in the Figures~\ref{fig:fliplink_orig} and \ref{fig:fliplink_changed}.
\begin{figure}[H]
    \begin{minipage}[t]{0.45\textwidth}
        \centering
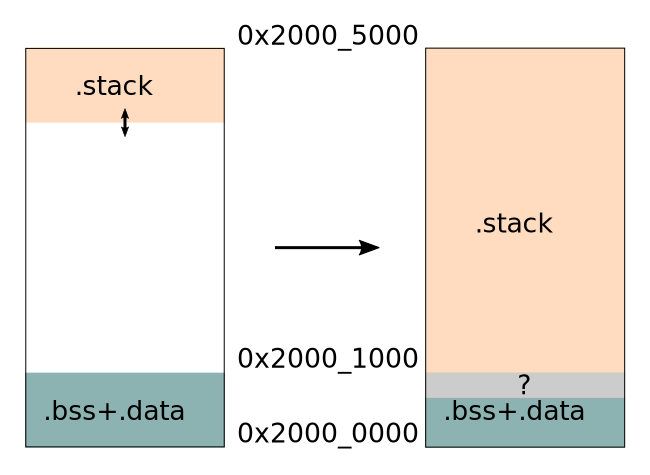
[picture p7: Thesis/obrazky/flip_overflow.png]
        
        \caption{Memory arrangement which causes memory corruption on stack overflow\cite{knurling_project_knurling-rsflip-link_2021}.}
        \label{fig:fliplink_orig}
    \end{minipage}\hfill
    \begin{minipage}[t]{0.45\textwidth}
        \centering
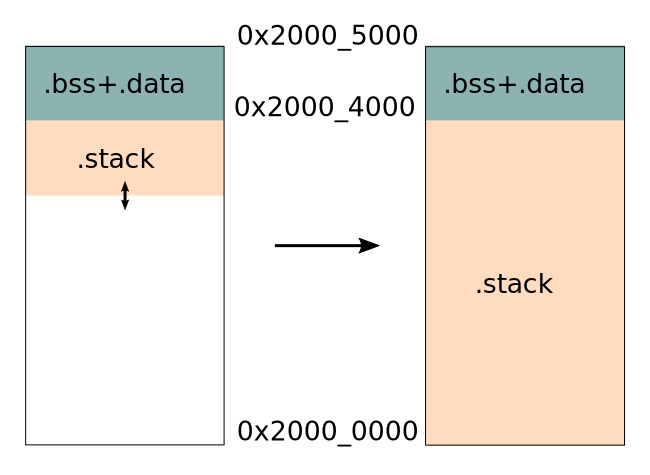
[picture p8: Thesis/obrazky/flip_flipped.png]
        
        \caption{Memory arrangement which causes hardware exception instead of corrupted memory\cite{knurling_project_knurling-rsflip-link_2021}.}
        \label{fig:fliplink_changed}
    \end{minipage}
\end{figure}

\subsection{Testing and CI}
\label{subsec:testing_ci}
While we already talked about testing in the Sections~\ref{subsec:testing} and \ref{subsubsec:defmttest}, we believe that there is more information about testing embedded Rust software and \acs{ci} (\acl{ci}).

There are two different types of tests that can be run for embedded software - tests that can be run without the hardware and tests that must be run on the target hardware as the code is dependent on it.
The tests that are independent of the target hardware can be tested using the standard Rust testing harness via, for example, \textbf{cargo test}, on the other hand, to run these tests, a target that supports \textbf{std} is required, which might require some project structure changes.
As for the tests that must run on the target hardware, the \textbf{defmt-test} test harness can be utilized.
Approaches for testing these parts of the embedded firmware can be found here\cite{aparicio_testing_nodate,aparicio_testing_nodate-1}.
Hardware in the loop-testing is also possible\cite{schievink_running_nodate}.

Nowadays, it is also possible to run the tests as part of the project's \acs{ci} workflow.
Apart from running tests, it is also possible to easily build the firmware itself as the only thing required is the Rust compiler with proper toolchain installed\cite{vahter_release_nodate}.
It is also possible to release the firmware, generate documentation and perform additional code checks on the codebase\cite{chiovoloni_few_2020}.

\newpage
\section{Embedded Rust Advantages and Disadvantages}
\label{sec:embedded_rust_reasoning}
Many of the reasons why we believe that Embedded Rust is the right choice for embedded development have already been described in the previous sections, but let us sum up what we believe are the most important points.
\begin{itemize}
    \item The Rust language promotes and ensures code that is not prone to memory safety problems and data races.
    \item The Rust language ecosystem is large, and integration of libraries is seamless and promotes code reuse.
    \item There are advanced and modern features in the language, making it easier to write safer and more expressive code.
    \item A lot of the abstractions provided by the programming language are zero-cost, meaning that they consume no additional resources.
    \item The embedded Rust ecosystem is vast, and contains well-thought-out solutions to difficult problems in embedded - see Section~\ref{subsec:mut_shared_state} on \acs{rtic}.
    \item The embedded Rust teams seek to utilize the modern programming features, such as async/await and generics - see Section~\ref{subsec:async} on async/await.
    \item Some of the harder parts embedded are already developed and ready to use - such as USB and Ethernet drivers, with the community aiming to solve these hard problems having a language that helps mitigate common programming mistakes.
    \item The embedded tooling is gradually improving, and in some ways it has already surpassed tooling in classical embedded languages - see the Section~\ref{subsec:tooling} on the tooling.
    \item Testing embedded systems with the Rust language is developed, and testing the firmware is easy, even in the \acs{ci}.
\end{itemize}

On the other hand, there are some disadvantages of using embedded Rust:
\begin{itemize}
    \item The resulting binaries can be quite large (10s of kB), making it harder to run on lower-end \acs{mcu}s.
    \item The support for debugging using GDB exists but is not very ergonomic.
    \item The support for embedded in commonly used \acs{ide}s is low, and sometimes, for example, the automatic code completion of registers can fail.
\end{itemize}

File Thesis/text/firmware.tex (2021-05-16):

\section{Development of the Bare-Metal Firmware}
\label{sec:firmware}
This Section describes the development of the bare-metal firmware.
First, we go over the firmware architecture, describing the technology stack and the architecture itself.
Second, we go over some components of the firmware that are either crucial to the firmware, or their implementation stands out in any way.

\subsection{Firmware Architecture}
\label{subsec:firmware-arch}
Firmware architecture can be described in many ways.
We decided to show three ways to describe this firmware.
First, we describe the technology stack, describing what crates and libraries upon which we built the hardware.
These libraries have mostly been described in the Section~\ref{sec:embedded_rust}.
The technology stack can be seen in the Figure~\ref{fig:firmware_tech_stack}.
When we go from the bottom, to the top, we can see that we access the hardware \acs{mcu} via two crates - the \textbf{stm32-rs} used to access peripheral circuits of the \acs{mcu} and the \textbf{cortex-m} crate used to access the \acs{arm} core of the \acs{mcu}.
The \textbf{stm32f4xx-hal} builds upon the \textbf{stm32-rs} crate and provides Hardware Abstraction Layer over the STM32F4 family and implements the \textbf{embedded-hal} traits.
The \textbf{cortex-m} crate is then used by the RTIC scheduler (described in the Section~\ref{subsec:mut_shared_state}).
As can be seen in the Figure, the firmware itself then builds upon all of these technologies - it accesses the HAL as some peripherals have their abstractions developed, for some special configurations, the direct peripheral register access via \textbf{stm32-rs} is used, the RTIC scheduler is used for orchestrating the firmware and for some low-level assembly instructions the \textbf{cortex-m} crate for low-level \acs{arm} core access is used.

\begin{figure}[H]
    \centering
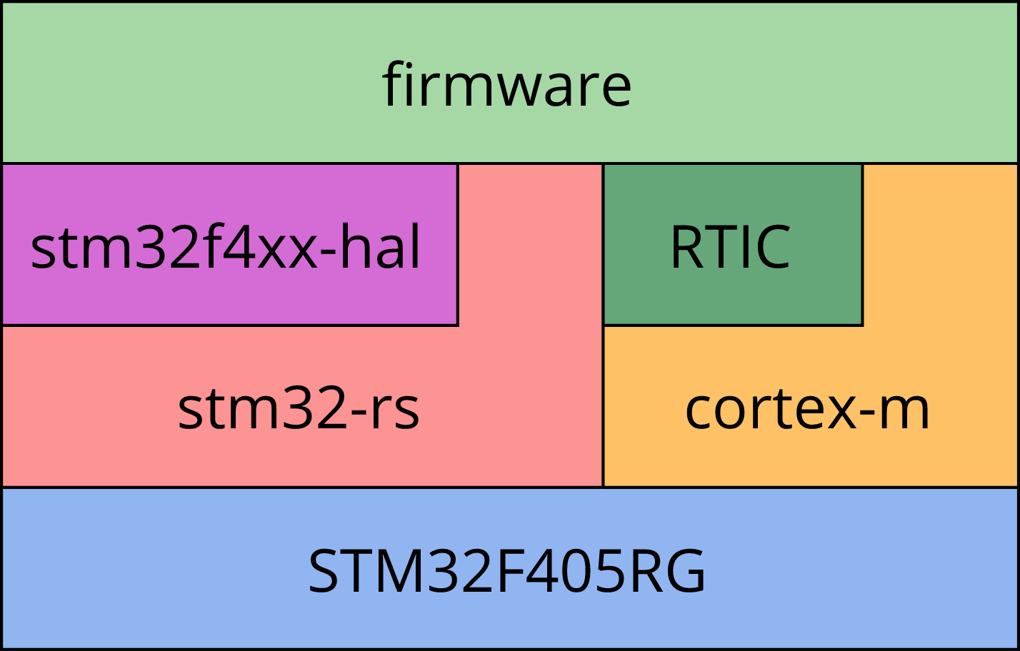
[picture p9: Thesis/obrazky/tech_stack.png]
    
    \caption{Bare\textendash metal firmware technology stack.}
    \label{fig:firmware_tech_stack}
\end{figure}

While the technology stack gives us vital information about the architecture, the architecture itself is much more complex and, in theory, could and should be independent of the used technologies\cite{thomas_pragmatic_2019}.
The architecture overview diagram can be seen in the Figure~\ref{fig:firmware_arch}.
The central part of the architecture is the Object Dictionary (described in Section~\ref{subsec:object_dictionary} and~\ref{subsec:object_dict_impl} (implementation-wise)).
The object dictionary contains the state of the stepper motor controller alongside configuration.
Part of the object dictionary is also persistent storage where its values are retained between reboots.
In the center of the firmware, there is also a general state that stores variables outside the scope of the Object Dictionary and software failsafe mechanisms that can manipulate bot the state and object dictionary.
When we look lower in the diagram, we can see that there are communication interfaces that receive data from and send them to the outer world, usually to some high-level system.
On the other hand, when we look higher in the diagram, that's where the motion control systems operate.
They get their data from the object dictionary (control values) and encoders and use them to control the stepper motor driver \acs{ic}s.
The encoders and motor drivers are again connected to the outer world - meaning that they interact with it via the connected motors.

\begin{figure}[H]
    \centering
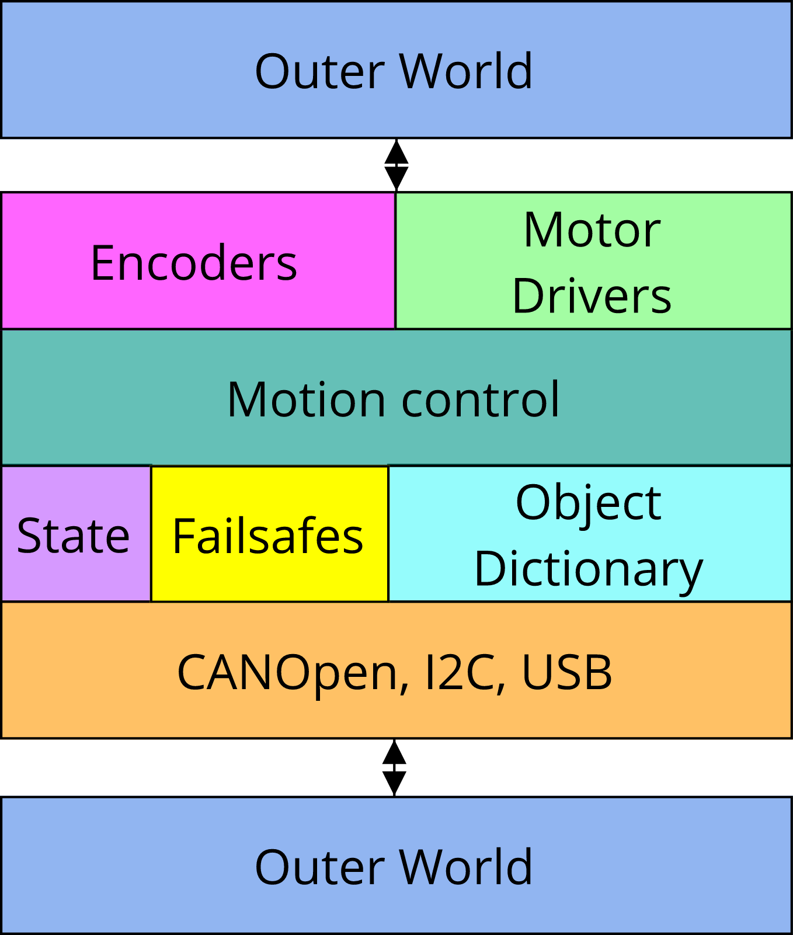
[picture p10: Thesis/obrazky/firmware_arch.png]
    
    \caption{Bare\textendash metal firmware architecture.}
    \label{fig:firmware_arch}
\end{figure}

There is one more final point of view on the architecture, connected with the project structure.
Given there are two projects - the bare-metal firmware and the further-described control application, there is a need to share code between those two projects, e.g., share communication models.
An vital distinction being that the bare-metal firmware is also cross-compiled in a \textbf{no\_std} environment.
Code sharing was solved by creating another project, that is \textbf{no\_std} and is called \textbf{shared}, both of the application projects statically link against it.
This can be seen in a diagram presented in the Figure~\ref{fig:component_arch}.
We adopted the project structure from\cite{aparicio_testing_nodate}, which proposes a project structure that promotes code sharing and testability of all components.

\begin{figure}[H]
    \centering
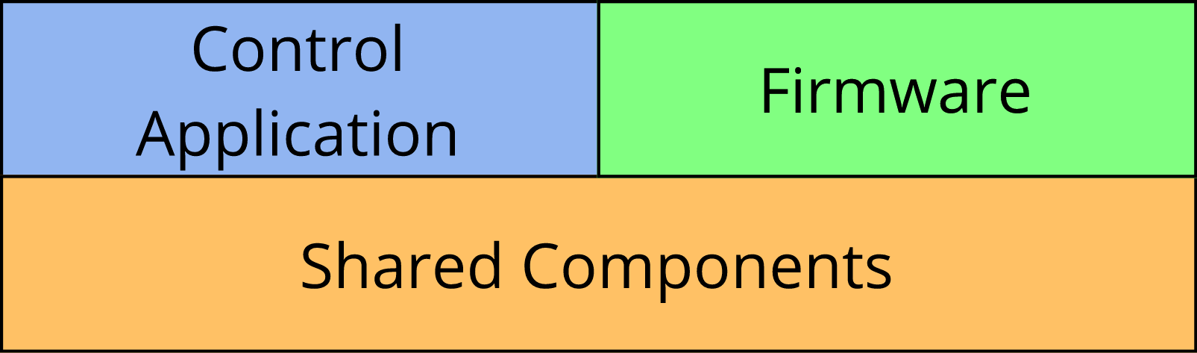
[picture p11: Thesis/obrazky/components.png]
    
    \caption{Component sharing between the bare\textendash metal firmware and the Control Application.}
    \label{fig:component_arch}
\end{figure}

\subsection{Object Dictionary}
\label{subsec:object_dict_impl}
The importance and role of the Object Dictionary was described in the Sections~\ref{subsec:object_dictionary} and~\ref{subsec:firmware-arch}.
When designing the Object Dictionary, we wanted to design it to be universally used and implemented in multiple ways (e.g., with persistent storage or without one).
The abstraction was done using traits.
The most important trait is the ObjectDictionary trait displayed in the Listing~\ref{lst:od_trait}.
This trait describes the Object Dictionary as a type that contains information about battery voltage, temperature, and an arbitrary number of axes.
The axis is also represented as a trait with accessor methods for specific axis settings (controller settings, current settings, etc.).

\newpage
\begin{lstlisting}[caption={Trait for abstracting away the Object Dictionary.},label=lst:od_trait]
/// Trait for Object Dictionary abstraction
pub trait ObjectDictionary<const RESOLUTION: u32> {
    /// Returns battery voltage stored in the Object Dictionary.
    fn battery_voltage(&self) -> f32;
    /// Returns temperature stored in the Object Dictionary.
    fn temperature(&self) -> f32;
    /// Sets the battery voltage value in the Object Dictionary.
    fn set_battery_voltage(&mut self, battery_voltage: f32);
    /// Sets the temperature value in the Object Dictionary.
    fn set_temperature(&mut self, temperature: f32);
    /// Returns the configuration of a specific axis.
    fn axis(&self, axis: Axis) -> &dyn AxisDictionary<RESOLUTION>;
    /// Returns a mutable reference the configuration of a specific axis.
    /// This is the only way an axis configuration can be changed
    fn axis_mut(&mut self, axis: Axis) -> &mut dyn AxisDictionary<RESOLUTION>;
}
\end{lstlisting}

To implement a simple Object Dictionary, implementing these traits would be enough.
Still, since we wanted to create an Object Dictionary whose values can be saved in arbitrary storage, we needed to create another abstraction for storage.
Such abstraction can be found in the Listing~\ref{lst:storage_trait}.
As can be seen in the Listing, the trait defines loading and saving values of 32-bit floats and boolean values for an arbitrary type of key that implements the ObjectDictionaryKey.

\newpage
\begin{lstlisting}[caption={Trait for abstracting away the Object Dictionary storage.},label=lst:storage_trait]
pub trait ObjectDictionaryStorage {
    fn save_f32<KEY: ObjectDictionaryKey>(&mut self,
        key: KEY, value: f32);
    fn save_bool<KEY: ObjectDictionaryKey>(&mut self,
        key: KEY, value: bool);
    fn load_f32<KEY: ObjectDictionaryKey>(&self,
        key: KEY) -> Option<f32>;
    fn load_bool<KEY: ObjectDictionaryKey>(&self,
        key: KEY) -> Option<bool>;
}
\end{lstlisting}

Using all the aforementioned traits, we then developed an Object Dictionary implementation called the PersistentStoreObjectDictionary, which is generic over the ObjectDictionaryStorage, meaning that an arbitrary storage type can be used with it.
Similar to the Object Dictionary traits, we also needed to develop a Persistent Store Object Dictionary for axis data, which is also generic over the Object Dictionary Storage and can be seen in the Listing~\ref{lst:persistent_store_dict}.

An important note is that now when any part of the code needs to access the Object Dictionary, it is done by hiding the real implementation behind dynamic dispatch based on the ObjectDictionary trait.

Since we are expecting that the only way a value can be written into the Object Dictionary is using the accessor methods, we employ buffering to make storage reads more scarce, therefore more making the ObjectDictionary more effective.
This basically means that at the firmware startup, all the values are loaded to \acs{ram}, and the storage is not accessed when reading.

\newpage
\begin{lstlisting}[caption={Object Dictionary for persistently storing axis data.},label=lst:persistent_store_dict]
#[derive(Copy, Clone)]
pub struct PersistentStoreAxisDictionary<
    STORAGE: 'static + ObjectDictionaryStorage,
    const RESOLUTION: u32,
> {
    axis: Axis,
    mode: AxisMode,
    enabled: bool,
    target_velocity: Velocity,
    actual_velocity: Velocity,
    target_position: Position<RESOLUTION>,
    actual_position: Position<RESOLUTION>,
    current: CurrentSettings,
    velocity_controller_settings: ControllerSettings,
    position_controller_settings: ControllerSettings,
    velocity_feedback_control_enabled: bool,
    acceleration: f32,
    storage: &'static Mutex<RefCell<STORAGE>>,
}
impl<STORAGE: 'static + ObjectDictionaryStorage, const RESOLUTION: u32>
    AxisDictionary<{ RESOLUTION }> for PersistentStoreAxisDictionary<STORAGE, RESOLUTION>
{
    fn set_accelerating_current(&mut self, current: f32) {
        self.current.set_accelerating_current(current);
        self.storage.lock().borrow_mut().save_f32(
            Key::key_for_axis(AxisKey::AcceleratingCurrent, self.axis),
            current,
        );
    }
...
}
\end{lstlisting}

\subsection{Persistent Storage Using EEPROM Emulation}
\label{subsec:eeprom}
In the previous Section, we discussed the development of storage-agnostic persistent Object Dictionary, and in this section, the way we implemented the persistent storage is described.
Persistent storage on MCUs is generally solved by using non-volatile memory that can be either part of the MCU or an external component.
Different memory technologies may be used for both types of storage.
In general, \acs{fram} (\acl{fram}), \acs{eeprom} (\acl{eeprom}), or flash memories are used.

To save space on the \acs{pcb}, save cost, and better utilize the MCU resources, we decided to use the internal flash memory to store the user data apart from the driver firmware.
Even though flash memory may seem straightforward to use since they are ubiquitous, its low-level use is not that simple.
Flash memory is generally divided into sectors that can be several kilobytes or megabytes large.
These sectors can be electrically erased - which means that every bit in the sector is set to 1.
Depending on the memory, a word of a specific size can be programmed, but it is only possible to flip the bits in the word to zero~\cite{mansanet_ecorax_nodate, mansanet_ecorax_nodate-1}.
The sector needs to be first erased and then programmed to write a higher number to the word in the sector.
This is problematic for two reasons:
\begin{enumerate}
    \item sectors generally have the size of several kilobytes, meaning that when you'd want to update the value in the desired word, the whole sector would have to be read to some other memory, erased, and then programmed again with the new, updated value,
    \item there is a limited number of the whole sector erases, caused by the limitation of the hardware.
\end{enumerate}

Fortunately, this problem can be solved by emulating the EEPROM memory as described in ST Application Note AN3969~\cite{stmicro_an3969_2011}.
The application note leverages two FLASH sectors of the same size, where one of them is marked as the active one and the second one is used when the first sector is full.
The working principle is described in the following paragraphs and can be seen in the Figure~\ref{fig:eeprom_emul}.

In the beginning, both of the sectors are erased, and one of them is marked as active.
Data are then written to the first sector into simulated cells.
The cells contain a header (which can be understood as a key or a virtual address) and the data.
When a new write is requested, the data are appended behind the already stored data.
When data is read using the virtual address, or a key, the sector is traversed from its end, searching for the first occurrence of the key or address.
The first occurrence is the most recent value of the cell marked by the key.
This way, we are able to store the value with a specific identifier (key, virtual address) in the flash multiple times.

When no more cells can be written to the active sector, the second sector is marked active.
The data are transmitted to the second sector, taking only the latest value of an identifier into account.
After the transfer, the first sector is erased.

\begin{figure}[H]
    \centering
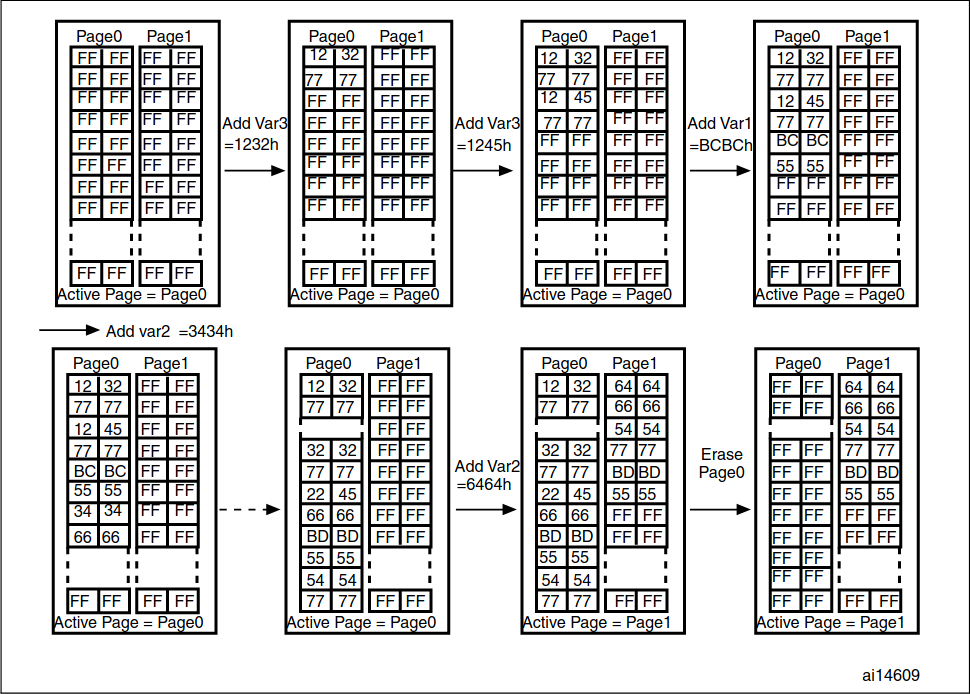
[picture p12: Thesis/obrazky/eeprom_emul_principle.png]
    
    \caption{EEPROM emulation working principle~\cite{stmicro_an3969_2011}.}
    \label{fig:eeprom_emul}
\end{figure}

Even though the working principle of the EEPROM emulation is simple, there are some technical obstacles in the implementation.
The first obstacle is that the flash memory on the STM32 MCU is split into differently sized sectors, and it is required that the sectors have the same size.
Referring to the Reference Manual~\cite{stmicro_stm32f405rg_nodate} there are some 16~kilobyte sectors that could be used for the emulation, as can be seen in the Figure~\ref{fig:flash_layout}.
Using the 128~kilobyte sectors would also be possible, but given their size, copying values from one sector to another would take too much time, and also, read access times would be higher.

\begin{figure}[H]
    \centering
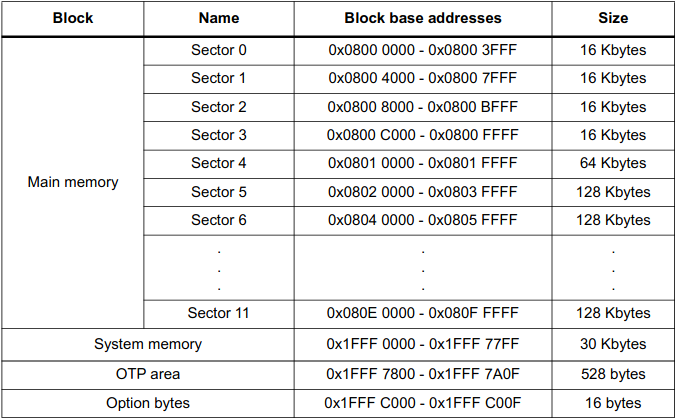
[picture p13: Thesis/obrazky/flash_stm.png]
    
    \caption{FLASH layout of the STM32F405 MCU~\cite{stmicro_stm32f405rg_nodate}.}
    \label{fig:flash_layout}
\end{figure}

There is, however a problem with using the sectors in the beginning of the flash memory as that is where the firmware is usually stored.
The solution to this problem is by leaving the first sector (Sector 0) for the vector table and instructing the linker to place the \textbf{.text} section of the program further in the memory.
According to the documentation of the \textbf{cortex-m} Rust crate~\cite{rust_embedded_devices_wg_rust-embeddedcortex-m_2021}, this can be achieved by adding the line \textbf{\_stext = ORIGIN(FLASH) + OFFSET} to the linker script, where the \textbf{OFFSET} shall be replaced with the offset of the target sector where we want our program to be stored, in our case \textbf{0x0000C000}, which indicates the start of the Sector 3.

As for the actual implementation of the emulation for the STM32F405, we decided to develop our own, as no suitable Rust crate was available for it.
The development was inspired by a crate that implemented the emulation for STM32F103~\cite{dubrov_idubroveeprom_2020} and by following the implementation in the Application Note.
The functions from flash memory access were adopted from an as of the time of writing unmerged Pull Request into the STM32F4 HAL~\cite{astro_implement_2020}.
An example of accessing the emulated persistent storage can be seen in the following Listing~\ref{lst:eeprom}.

\newpage
\begin{lstlisting}[caption={An example use of the emulated persistent storage.},label=lst:eeprom]
let mut store = Storage::new(device.FLASH);
store
    .init()
    .expect("Failed to initialize emulated storage.");
store.write_f32(0xbeef, 3.14);
let read = store.read_f32(0xbeef).unwrap();
assert_eq!(read, 3.14);
\end{lstlisting}

As can be seen in the Listing~\ref{lst:eeprom}, first we create the object with a parameter of the flash peripheral, then we initialize the emulated storage - this prepares the sectors that are supposed to be used, and then we perform a simple write and read operations on the storage.

\subsection{CANOpen Implementation}
\label{subsec:canopen_impl}
The CAN bus on STM32 is implemented in hardware in the bxCAN peripheral.
This peripheral is the same for all of the STM32F \acs{mcu}s, only with slight differences in filter banks and message mailbox sizes.
Given this fact, it was possible to develop a crate that supports all of the STM32 \acs{mcu}s, the crate is called \textbf{bxcan} and is developed the stm32-rs organization.

In the past projects described in Chapter~\ref{ch:related_work}, we utilized our own implementation of a driver for the bxCAN peripheral, but since the \textbf{bxcan} crate is well maintained, documented, and tested, we decided to discontinue the development of the driver and migrate to \textbf{bxcan}.

In order to implement the CANOpen protocols described in the Section~\ref{subsec:canopen}, we developed a simple wrapper over the \textbf{bxcan} crate.
The wrapper is basically a simple proxy that transforms CANOpen protocol data to CAN frames and sends them and parses received CAN frames into CANOpen protocol data.
Upon initialization, the wrapper first configures the bxCAN peripheral, enables interrupts, and enables the peripheral itself.

The bxCAN initialization in the wrapper can be seen in the Listing~\ref{lst:canopen_wrapper}.
\newpage
\begin{lstlisting}[caption={Initializing the bxCAN peripheral in the CANOpen wrapper.},label=lst:canopen_wrapper]
let mut bus = Can::new(bus);
bus.configure(|config| {
    config.set_bit_timing(0x001a000b);
});
bus.enable_interrupts(
    Interrupts::FIFO0_MESSAGE_PENDING | Interrupts::FIFO1_MESSAGE_PENDING,
);
bus.modify_filters()
    .clear()
    .enable_bank(0, Mask32::accept_all());
bus.set_automatic_wakeup(true);
nb::block!(bus.enable()).unwrap();
\end{lstlisting}

When an interrupt handler is invoked, the function \textbf{process\_incoming\_frame} is called, and it returns the type of the CANOpen protocol message alongside with received frame.
If the frame contains a valid CANOpen message, the CAN frame is further parsed, for example, to decode the contents of the PDO as can be seen in the Listing~\ref{lst:can_parse}
In the Listing, we can also see accessing the generic ObjectDictionary via the structure \textbf{DriverState}.
\newpage
\begin{lstlisting}[caption={Accessing the Object Dictionary when a RxPDO2 is received.},label=lst:can_parse]
pub fn rx_pdo2<OD, const R: u32>(frame: &Frame, state: &mut DriverState<OD, R>)
where
    OD: ObjectDictionary<R>,
{
    if frame.data().is_none() {
        defmt::warn!("Invalid RxPDO2 received.");
        return;
    }
    if let Ok(pdo) = RxPDO2::try_from(frame.data().unwrap().as_ref()) {
        state
            .object_dictionary()
            .axis_mut(Axis::Axis1)
            .set_target_velocity(Velocity::new(pdo.axis1_velocity));
        state
            .object_dictionary()
            .axis_mut(Axis::Axis2)
            .set_target_velocity(Velocity::new(pdo.axis2_velocity));

        state.invalidate_last_received_speed_command_counter();
    } else {
        defmt::warn!("Malformed RxPDO2 received.");
    }
}
\end{lstlisting}

\subsection{I\textsuperscript{2}C Slave Implementation}
\label{subsec:i2c_impl}
Implementing I\textsuperscript{2}C slave on a \acs{mcu} is a cumbersome problem, as there is not enough documentation or example code.
Timing of the bus, requiring the slave to react within relatively short time, makes development and debugging harder.
On the other hand with the help of \textbf{defmt} and \acs{rtt} this is not a problem anymore.
We had already developed one implementation of the I\textsuperscript{2}C Slave handling for STM32F0 \acs{mcu} as a part of the KM3 firmware described in the Section~\ref{sec:km3}.
Unfortunately, the STM32F4 family has a different version of the I\textsuperscript{2}C peripheral than the STM32F0, resulting with significant changes to the peripheral handling code, even though the external \acs{api} remained the same.
The I\textsuperscript{2}C2 peripheral is utilized, and it is configured to use the 7-bit addressing mode, with enabled clock stretching to give the \acs{mcu} more time to prepare the data for transfer.
Finally, all the interrupt sources are enabled.
The peripheral has two interrupt vectors - one for data-related interrupts \textbf{I2C2\_EV} and one for error-related interrupts \textbf{I2C2\_ER}.
When the error-related interrupt handler is invoked, the error flags are cleared, and the transfer is reset.
In the data-related interrupt handler, the state machine implementing the I\textsuperscript{2}C slave register-based protocol (described in the Section~\ref{subsec:i2c}) is implemented.
The result of calling the data interrupt handling function is a state which denotes what is expected by the higher-level system - the data can be either requested or received.
The upper-level system then handles transferring the data between the I\textsuperscript{2}C slave implementation's buffers and the Object Dictionary.

\subsection{USB}
\label{subsec:usb_impl}
The integrated \acs{usb} on the SM4 stepper motor controller has two functions - it enables the possibility to upgrade the firmware via \acs{dfu} (handled by the internal \acs{mcu} bootloader) and provides an interface for configuration (developed by us in the firmware).
For the configuration, the \acs{usb} utilizes the CDC-ACM device class, which means that to the host device, the SM4 controller turns up as a serial port.
Thankfully, given the ubiquity of \acs{usb} devices, crates for implementing \acs{usb} devices on the STM32 are already developed.
There is the crate \textbf{usb-device} providing the \acs{usb} stack and abstractions for hardware\cite{virkkunen_mvirkkunenusb-device_2021}, the \textbf{stm32-usbd}\cite{noauthor_stm32-rsstm32-usbd_2021} implementing the hardware abstraction and \textbf{usbd-serial}\cite{virkkunen_mvirkkunenusbd-serial_2021} implementing the CDC-ACM device class for the \textbf{usb-device} stack.

The implementation of this functionality in the firmware is done via the \textbf{USBProtocol} struct, which is basically a wrapper over the raw USB Serial port functionality.
This wrapper is interrupt-driven, quite similarly to the I\textsuperscript{2}C Slave driver, meaning that the received data is parsed when an interrupt handler is invoked, and the data is then exchanged between the wrapper and the Object Dictionary.

An example of configuring the \acs{usb} device can be found in the Listing~\ref{lst:usb}.
\newpage
\begin{lstlisting}[caption={Initializing the USB device with the CDC-ACM class.},label=lst:usb]
let usb_dev = unsafe {
    UsbDeviceBuilder::new(USB_BUS.as_ref().unwrap(), UsbVidPid(0x16c0, 0x05e1))
        .manufacturer("MH Robotics")
        .product("SM4")
        .serial_number("sm4202101")
        .device_class(usbd_serial::USB_CLASS_CDC)
        .build()
};
\end{lstlisting}
The used device \textbf{VID} and \textbf{PID} were adopted from the VUSB project\cite{noauthor_obdevv-usb_nodate}, that provides them for free with some rules about their use.

\subsection{Stepper control}
\label{subsec:stepper_control}
Movement of stepper motors, controlled using the stepper motor driver \acs{ic}s is generally controlled using the \textbf{STEP/DIR} interface.
This interface consists of two signals, the first of them named~\textbf{STEP} is a square wave signal with variable frequency, where the edges (rising, falling, or both) instruct the driver to move the motor by a microstep.
On the other hand, the second signal named \textbf{DIR} is generally a logic signal whose logic level denotes the direction of the shaft movement.

Apart from these two digital signals, there is usually an analog signal that is used to set the motor phase current.
In more modern stepper drivers, this analog signal is replaced by a serial digital interface, allowing for a finer current setting.

The \textbf{STEP} signal can be generated either in software (by changing the output logic level of a \acs{gpio} pin) or in hardware by utilizing a \acs{pwm} signal with the duty cycle of 50 \%.
Both of these approaches have their limitations and advantages.
Generating the signal in software has the advantage of being able to easily count the number of microsteps the motor was commanded to do.
On the other hand the upper limit of the maximal frequency is much lower than with hardware generation, and this technique uses more computational resources as the signal is generally generated using an interrupt on timer overflow, where the signal logic level needs to be toggled (which requires branching) and the pulse counter needs to be accessed.
Using a timer with \acs{pwm} allows for much higher maximal frequencies.
On the other hand counting the pulses can prove to be quite hard.
This issue will be described in more detail in the Section~\ref{subsec:simulated_encoders}.

We decided to utilize the \textbf{STEP} signal generation done by the hardware as we wanted to offload the work from the \acs{mcu} core.

To abstract the real implementation, we created a trait (see Section~\ref{subsec:traits}) for setting the microstepping frequency, as can be seen in the Listing~\ref{lst:step_gen_trait}.
Using this trait, the software controlling the stepper driver \acs{ic} can use either hardware or software \textbf{STEP} signal generator.

\begin{lstlisting}[caption={Trait for abstracting STEP generation.},label=lst:step_gen_trait]
/// This trait is an abstraction over hardware/software that is capable of generating square wave signal of specific frequency.
/// It is generally implemented by timers.
pub trait StepGenerator {
    /// Sets output frequency of the generator.
    ///
    /// # Arguments
    /// * `frequency` - frequency of the output square wave signal
    fn set_step_frequency(&mut self, frequency: Hertz);
}
\end{lstlisting}

In our case, the trait is implemented by the abstractions over the \acs{mcu}'s advanced control timers 1 and 8.
The abstractions over the timers are based on the timer implementations found in the \textbf{stm32f4xx-hal}, but are preconfigured to generate output \acs{pwm} signals and also to act as a master timer generating the clock signal for other timers on compare.

Using this trait, we were able to define a struct that describes the TMC2100 driver, as can be seen in the Listing~\ref{lst:tmc2100}.

\begin{lstlisting}[caption={TMC2100 driver.},label=lst:tmc2100]
pub struct TMC2100<G, STEP, DIR, DAC> {
    generator: G,
    _step_pin: STEP,
    dir_pin: DIR,
    current_dac: DAC,
    sense_r: f32,
    microsteps_per_revolution: f32,
}
\end{lstlisting}
In the Listing, we can see that the driver contains a generic generator, has ownership of the \textbf{STEP} pin (so that no other peripheral can access it), has ownership of the \textbf{DIR} pin, \acs{dac} current reference and knows the value of the sense resistor for current setting and microsteps per revolution for \textbf{STEP} output frequency setting.

For a more seamless integration with the motion controller described in the Section~\ref{subsec:motion_control} the trait \textbf{StepperDriver} was declared as can be seen in the Listing~\ref{lst:stepper_driver_trait}.

\begin{lstlisting}[caption={Trait for abstracting the stepper motor driver IC.},label=lst:stepper_driver_trait]
/// This trait is an abstraction over stepper drivers.
/// Generally the drivers have two functions - generate steps and set output current.
pub trait StepperDriver {
    /// Sets output frequency of the driver.
    /// this shall be the angular frequency of the output shaft in revolutions per second.
    ///
    /// # Arguments
    /// * `frequency` - frequency of the output motor shaft in revolutions per second
    fn set_output_frequency(&mut self, frequency: f32);

    /// Sets the target current the driver shall drive the stepper motor with.
    ///
    /// # Arguments
    /// * `current` - the desired current in Amps
    fn set_current(&mut self, current: f32);
}
\end{lstlisting}

This trait was then implemented for the TMC2100 structure, implementing the stepper control itself, as is shown in the Listing~\ref{lst:stepper_driver_impl}.

\newpage
\begin{lstlisting}[caption={Implementing the StepperDriver trait for TMC2100.},label=lst:stepper_driver_impl]
impl<G, STEP, DIR, DAC> StepperDriver for TMC2100<G, STEP, DIR, DAC>
where
    G: StepGenerator,
    DIR: embedded_hal::digital::v2::OutputPin,
    DAC: DACChannel,
{
    fn set_output_frequency(&mut self, frequency: f32) {
        if frequency < 0.0 {
            self.dir_pin.set_high().ok();
        } else {
            self.dir_pin.set_low().ok();
        };
        self.generator.set_step_frequency(Hertz::new(
            (frequency.abs() * self.microsteps_per_revolution) as u32,
        ))
    }
    fn set_current(&mut self, current: f32) {
        let voltage = (current.abs() * MAX_V_REF as f32 / V_FS * (self.sense_r + R_OFFSET) / 0.707) as u16;
        self.current_dac.set_output_voltage(voltage.min(MAX_V_REF));
    }
}
\end{lstlisting}

\subsection{Simulated encoders}
\label{subsec:simulated_encoders}
The SM4 stepper motor controller is meant to be used without a hardware encoder in its default hardware configuration.
This requirement was caused by the reasoning that the motor controller is also targeted for the BPC-PRP course, where students use the distance driven by the wheels to calculate the robot's position in the world's reference frame.
Thankfully, with a stepper motor, it is quite easy to simulate encoders by counting the number of microsteps the motor was supposed to move by.
The simulated encoders do not provide real feedback from the system
On the other hand, when some conditions are met (no step skipping - no motor overloading), the measurement from them can be quite reliable.

As we already discussed in the Section~\ref{subsec:stepper_control}, we decided not to use counting the microsteps in software but in hardware instead.
This is done by chaining timers in the \acs{mcu}.
We already mentioned that the timers used to generate \textbf{STEP} signal are configured to be the clock source for other timers, and by counting the clock cycles, we are able to count the number of microsteps the motor was commanded to turn by.

The working principle is really simple and also saves computational power of the \acs{mcu}, but has one disadvantage - the amount of microsteps per sampling period is too low to be used for velocity control, as the difference between the consecutive position reads is usually zero and only sometimes 1.
This poses a big problem for motor control systems of any kind.

Let's have a look at the implementation.
Similar to what we did with the \textbf{STEP} signal generators, we also declared a trait to abstract away the thing that counts the pulses so that on the outside, it doesn't matter how the counting works.
The trait can be seen in the Listing~\ref{lst:step_counter}.

\begin{lstlisting}[caption={Counter trait for counting STEP pulses.},label=lst:step_counter]
/// Trait used to abstract STEP pulse and other counters.
pub trait Counter {
    /// Return the current internal value of the counter.
    fn get_value(&self) -> u32;
    /// Resets the internal value of the counter.
    fn reset_value(&mut self);
}
\end{lstlisting}
The trait was implemented for timers 2 and 5 of the \acs{mcu}.

Apart from this trait, an abstraction over the whole encoded was developed.
The abstraction utilizes const generics to define encoder resolution and can be seen in the Listing~\ref{lst:encoder_trait}.

\newpage
\begin{lstlisting}[caption={Encoder trait for abstracting encoders.},label=lst:encoder_trait]
/// A trait abstracting common encoder functionality.
/// It is suitable for both incremental and absolute encoders.
/// It is designed so its [`Self::sample()`] shall be periodically called with known fixed period,
/// which allows for velocity calculations.
pub trait Encoder<const RESOLUTION: u32> {
    /// Returns the velocity measured by the encoder.
    /// This value is generally calculated from consecutive position readings.
    fn get_velocity(&self) -> Velocity;
    /// Returns the current position of the shaft.
    fn get_position(&self) -> Position<RESOLUTION>;
    /// Sets the sampled position to zero.
    /// This is applicable only with incremental encoders.
    /// Absolute encoders might offset the zero by software.
    fn reset_position(&mut self) -> Position<RESOLUTION>;
    /// This function shall be periodically called to sample the encoder.
    /// Sampled values are used for position and velocity readings.
    fn sample(&mut self);
    /// This method shall be called with non-directional encoders whenever there is a change of rotation direction.
    /// # Arguments
    /// * `direction` - indicates whether the shaft is now turning in the clockwise or counterclockwise direction.
    fn notify_direction_changed(&mut self, direction: Direction);
}
\end{lstlisting}

Based on this trait and the Counter trait, a simulated encoder was developed.
The big advantage is that the simulated encoder can be easily replaced by another hardware or software realized encoders.
This Encoder trait is further used in the motion controller.

For representing the position, we utilized the model used in servo controllers by TGDrives - a signed integer denoting the number of revolutions and an unsigned integer indicating the angle.
For example, assume that we have a two-bit encoder, and a position of 1 revolution, and the angle with the value of 2, meaning that the position is equal to 1.5 revolutions.
Now, assume that the number of revolutions is -1, and the angle is again 2, which means that the resulting position represented by these two numbers is -0.5.
More on this implementation, alongside with tests, can be found in the shared library in the module defining the structure Position.

\subsection{Device Monitoring}
\label{subsec:device_monitoring}
In order to provide status and health information, simple device monitoring is employed.
The monitoring system periodically reads internal \acs{mcu} temperature and the motor voltage.
This functionality is implemented by accessing the internal \acs{mcu} \acs{adc}.
The internal \acs{adc} utilizes the Successive approximation principle and supports up-to 19 channels\cite{stmicro_stm32f405xx_2020}.
The \acs{adc} is configured to read the two channels and to use \acs{dma} to transfer the values from the peripheral to the program's memory.
Both \acs{adc} configuration and \acs{dma} transfer are already implemented in the \textbf{stm32f4xx-hal} crate, meaning that no low-level peripheral access code was required.
The monitoring data are periodically transferred to the Object Dictionary by the higher-level code.

First, we configure the \acs{adc} as can be seen in the Listing~\ref{lst:adc}.
We set the \acs{dma} transfer mode to \textbf{Continuous} (which reissues a \acs{dma} request on every start of conversion) and enable scan mode, which scans all the channels in the sequence.
Further, both of the channels are configured, with the assignment to pin or special channel, the order in the conversion sequence, and sample time, which denotes for how many clock cycles the sample-and-hold circuits samples.
Finally, the temperature and VRef channel measurement is enabled as it is not enabled by default by the hardware.

\newpage
\begin{lstlisting}[caption={Configuring ADC for temperature and voltage monitoring.},label=lst:adc]
let mut adc = Adc::adc1(raw_adc, true, adc_config);
let adc_config = AdcConfig::default()
     .dma(Dma::Continuous)
     .scan(Scan::Enabled);
adc.configure_channel(&Temperature, Sequence::One, SampleTime::Cycles_480);
adc.configure_channel(&battery_voltage, Sequence::Two, SampleTime::Cycles_480);
adc.enable_temperature_and_vref();
\end{lstlisting}

Next, we configure the \acs{dma} transfer, as can be seen in the Listing~\ref{lst:dma}.
We configure the \acs{dma} controller to issue an interrupt when the transfer is complete, to increment addresses only in memory and not in the peripheral, and we disable double buffering.

\begin{lstlisting}[caption={Configuration of the DMA controller for ADC transfers.},label=lst:dma]
let first_buffer = singleton!(: [u16; 2] = [0; 2]).unwrap();
let config = DmaConfig::default()
    .transfer_complete_interrupt(true)
    .memory_increment(true)
    .double_buffer(false);
let transfer = Transfer::init(dma, adc, first_buffer, None, config);
\end{lstlisting}

The monitoring system is then periodically asked to poll data from the \acs{adc} by starting the transfer as can be seen in the following Listing~\ref{lst:adc_poll}.
\begin{lstlisting}[caption={Polling the ADC.},label=lst:adc_poll]
self.transfer.start(|adc| {
    adc.start_conversion();
});
\end{lstlisting}
When the \acs{dma} transfer complete interrupt routine is called, the subsequent transfer is prepared, and the measured data is processed using factory calibration and formulae that can be found in the reference manual\cite{stmicro_stm32f405xx_2020}.
The final two coefficients in the battery\_voltage calculation represent the voltage divider described in the Section~\ref{subsec:aux_connectors}.
The preparation and calculation is shown in the Listing~\ref{lst:adc_isr}.

\newpage
\begin{lstlisting}[caption={Processing the data measured by the ADC.},label=lst:adc_isr]
let (buffer, _) = self
    .transfer
    .next_transfer(self.buffer.take().unwrap())
    .unwrap();
let raw_temp = buffer[0];
let raw_volt = buffer[1];
self.buffer = Some(buffer);
let cal30 = VtempCal30::get().read() as f32;
let cal110 = VtempCal110::get().read() as f32;
self.temperature = (110.0 - 30.0) * ((raw_temp as f32) - cal30) / (cal110 - cal30) + 30.0;
self.battery_voltage = (raw_volt as f32) / ((2_i32.pow(12) - 1) as f32) * 3.3 / 4.7 * 104.7;
\end{lstlisting}

\newpage
\subsection{Motion Control}
\label{subsec:motion_control}
Motion control is a crucial component of the firmware.
Based on the values stored in the Object Dictionary, it calculates the output control signal values for the stepper motor driver \acs{ic}s.
In our case, the core of the motion control component are two nested PSD controllers.
The controllers are implemented with anti-windup realized by summator and output value clamping
The algorithm used for the PSD controller can be seen in the Listing~\ref{lst:psd}.
For ease of use, all the constants are stored in a structure \textbf{ControllerSettings}.
\begin{lstlisting}[caption={Implementation of the PSD controller with integrator.},label=lst:psd]
let error = desired - actual;
self.sum += error * self.sampling_period;
self.sum = self.sum.clamp(
    -settings.max_output_amplitude,
    settings.max_output_amplitude,
);
let action = error * settings.proportional
    + settings.derivative * (error - self.previous) / self.sampling_period
    + settings.integral * self.sum;
self.previous = error;
action.clamp(
    -settings.max_output_amplitude,
    settings.max_output_amplitude,
)
\end{lstlisting}

One of these controllers (the inner one) is used for controlling output speed based on the target speed, and the second one (the outer one) is used to control the position.
The structure of the motion controller can be seen in the Figure~\ref{fig:motion_control}.

\begin{figure}[H]
    \centering
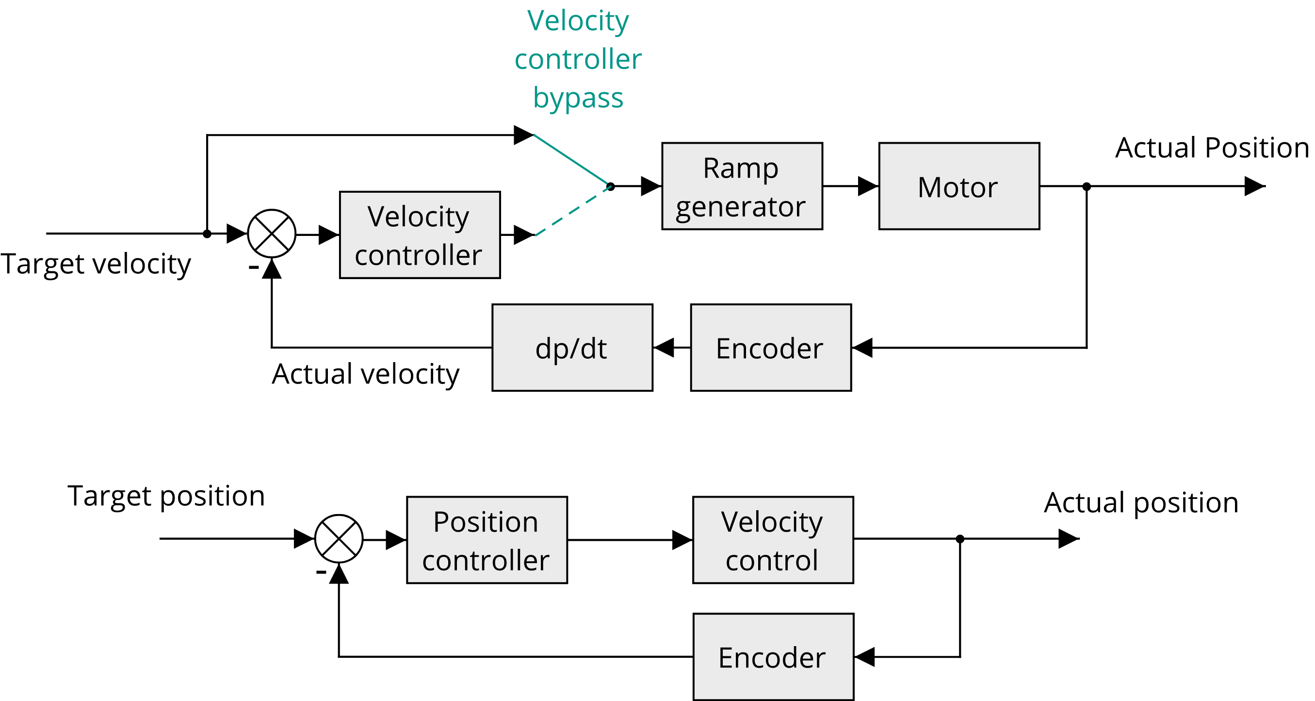
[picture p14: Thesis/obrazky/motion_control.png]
    
    \caption{Motion control schematic.}
    \label{fig:motion_control}
\end{figure}

In the first half of the Figure, there is the velocity controller, which is used both when the SM4 stepper motor controller's axis is running in the velocity or position mode.
Given that the stepper motor controllers are often driven in the open-loop, there is an option to bypass the velocity PSD controller, meaning that the target speed is directly passed to the ramp generator.
The ramp generator is capable of generating trapezoidal ramps with defined acceleration.
An important note being that the ramp generator is sampled at a higher frequency than the rest of the motion controller.
The algorithm for calculating trapezoidal ramps can be seen in the Listing~\ref{lst:ramp}.
\begin{lstlisting}[caption={Calculating trapezoidal ramps.},label=lst:ramp]
pub fn generate(&mut self, target_speed: f32, target_acceleration: f32) -> f32 {
    let step = target_acceleration / self.generation_frequency;
    let diff = target_speed - self.current_speed;
    if diff.abs() < step {
        self.current_speed = target_speed;
    } else {
        self.current_speed += diff.signum() * step;
    }
    self.current_speed
}
\end{lstlisting}

Velocity calculated by the ramp generator is then passed to the stepper motor driver \acs{ic} via an abstraction.
In the case of the closed-loop control, the bypass is not active, and the velocity controller regulates the velocity based on the value speed measured by the encoder.
It is important to note that to successfully control in closed-loop mode the difference between encoder samples must be higher than 0, ideally several orders of magnitude higher.

When the SM4 stepper motor controller's axis is running in the position control mode, the second controller shown in the second half of the Figure is utilized.
In this case, the feedback from the encoder is utilized and this controller is a proper closed-loop controller.

The actual motion controller implementation utilizes the \textbf{StepperDriver} and \textbf{Encoder} traits described in the Sections~\ref{subsec:stepper_control} and~\ref{subsec:simulated_encoders}.
It is declared as follows in the Listing~\ref{lst:mc_decl}.
\begin{lstlisting}[caption={Implementation of the PSD controller with integrator.},label=lst:mc_decl]
/// Motion controller of an arbitrary axis.
/// This motion controller expects that the target driver is controlled either in velocity or position mode.
/// Trapezoidal ramp generator is utilized.
pub struct AxisMotionController<D: StepperDriver, E: Encoder<RESOLUTION>, const RESOLUTION: u32> {
    /// The target stepper motor driver, that will be controlled by this motion controller.
    driver: D,
    /// The encoder, that will be used to provide feedback for closed loop control
    encoder: E,
    velocity_controller: PSDController,
    position_controller: PSDController,
    ramp_generator: TrapRampGen,
    /// Variable used to store the calculated velocity action for ramp generator.
    axis_velocity_action: f32,
}
\end{lstlisting}
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

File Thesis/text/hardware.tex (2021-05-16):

\section{Electronics Design}
\label{sec:hardware}

This section describes the electronics of the SM4 stepper motor controller.
First, the critical components are selected, and preliminary design is done based on the requirements stated in the Section~\ref{sec:requirements}.
Second, the design of the electronics is described.
There were two electronics revisions, where different stepper motor driver \acs{ic} was used in each of them.
In the description, the second revision is prioritized except for the design of the circuit of the stepper motor controller \acs{ic} where both of the revisions are described.
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

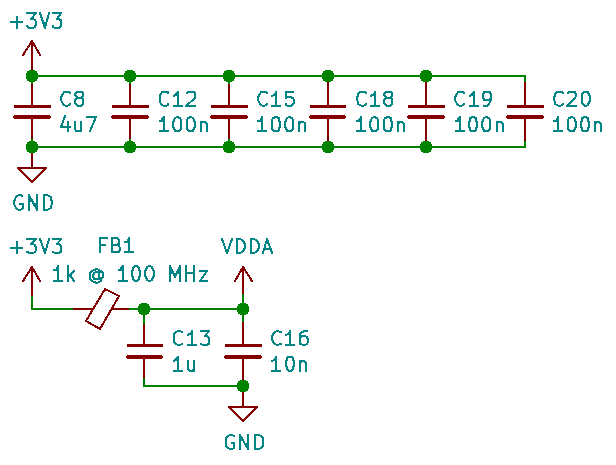
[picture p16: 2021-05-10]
Thesis/obrazky/schem_mcu_power_filter.png

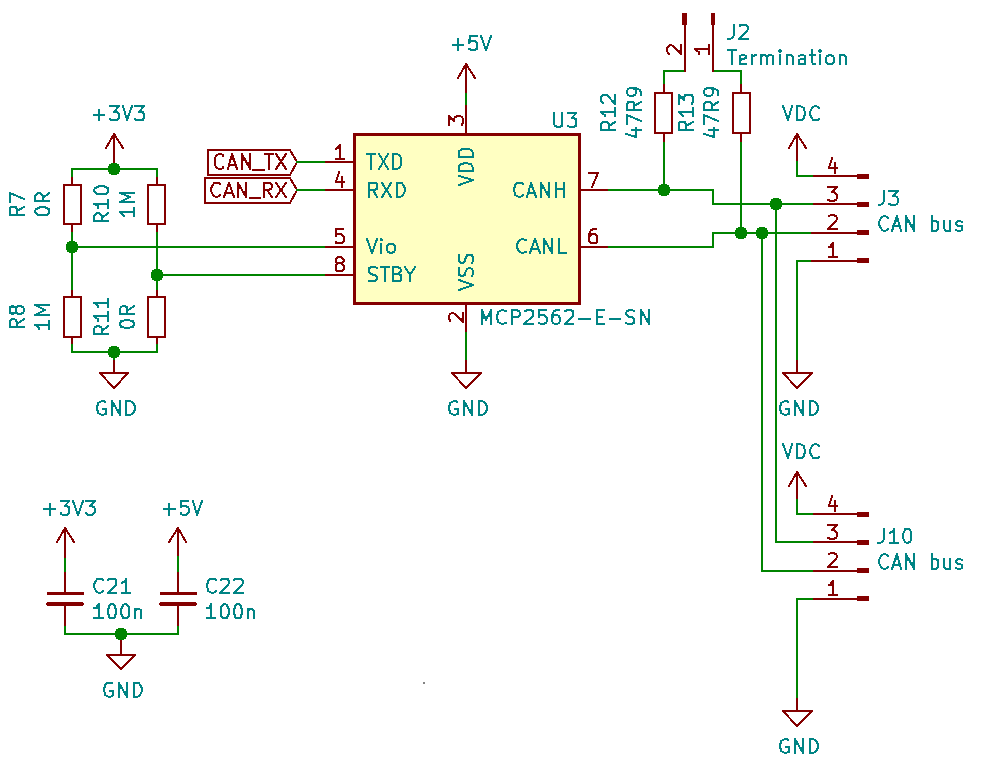
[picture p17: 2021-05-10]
Thesis/obrazky/schem_can.png

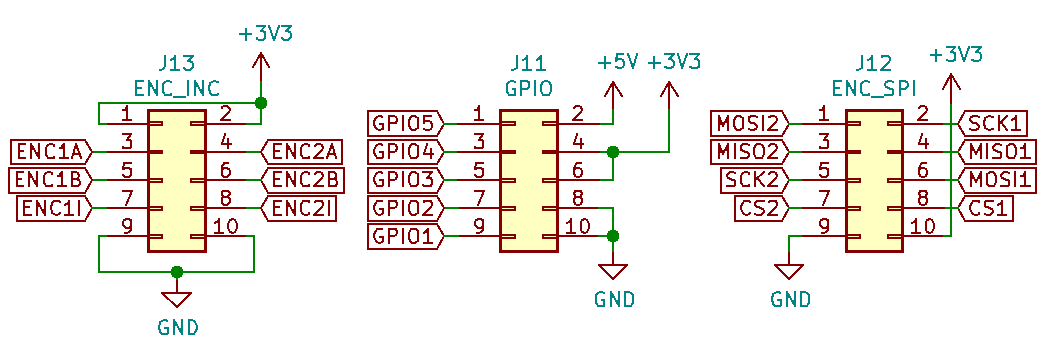
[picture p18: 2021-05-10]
Thesis/obrazky/schem_enc_gpio.png

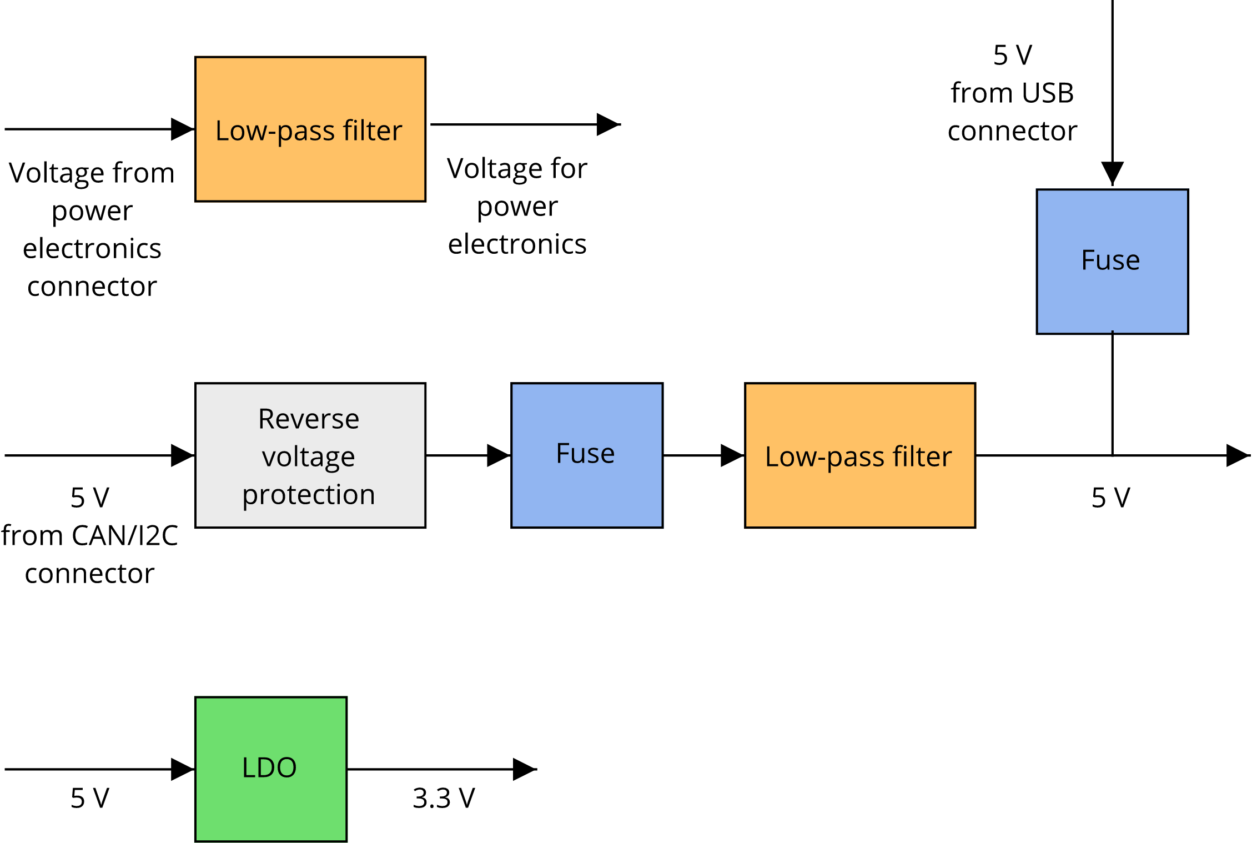
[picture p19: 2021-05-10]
Thesis/obrazky/power_block_diagram.png

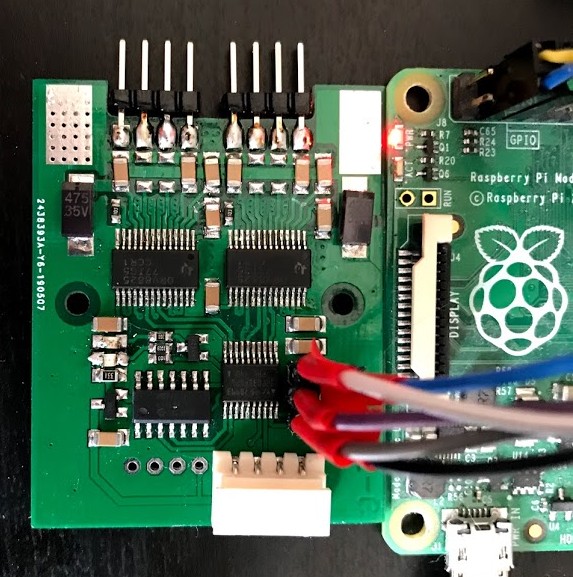
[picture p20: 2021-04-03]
Thesis/obrazky/km3.jpg

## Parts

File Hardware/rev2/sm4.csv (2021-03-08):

Comment | Designator | Footprint | LCSC
2u2 | C1,C5,C29,C33 | Capacitor_SMD:C_0603_1608Metric_Pad1.08x0.95mm_HandSolder | C23630
10n | C11 | Capacitor_SMD:C_0603_1608Metric_Pad1.08x0.95mm_HandSolder | C57112
100n | C12,C15,C18,C19,C20,C21,C22 | Capacitor_SMD:C_0402_1005Metric_Pad0.74x0.62mm_HandSolder | C1525
1u | C13,C34,C35 | Capacitor_SMD:C_0603_1608Metric_Pad1.08x0.95mm_HandSolder | C15849
12p | C14,C17 | Capacitor_SMD:C_0402_1005Metric_Pad0.74x0.62mm_HandSolder | C1547
10n | C16,C36 | Capacitor_SMD:C_0402_1005Metric_Pad0.74x0.62mm_HandSolder | C15195
100n | C2,C23,C45,C46,C48,C49 | Capacitor_SMD:C_0603_1608Metric_Pad1.08x0.95mm_HandSolder | C14663
1u | C25 | Capacitor_SMD:C_1206_3216Metric_Pad1.33x1.80mm_HandSolder | C1848
10u | C3,C4,C7,C9,C10,C24,C26,C27,C28,C31,C32,C37,C38,C39,C40,C41,C42,C43,C44,C47 | Capacitor_SMD:C_1206_3216Metric_Pad1.33x1.80mm_HandSolder | C13585
22n@50V | C6,C30 | Capacitor_SMD:C_0402_1005Metric_Pad0.74x0.62mm_HandSolder | C1532
4u7 | C8 | Capacitor_SMD:C_0603_1608Metric_Pad1.08x0.95mm_HandSolder | C19666
D_Small | D3,D4 | Diode_SMD:D_SOD-123 | C8598
LED_Small | D1,D5,D6,D7 | LED_SMD:LED_0603_1608Metric_Pad1.05x0.95mm_HandSolder | C72038
500mA | F1,F2 | Fuse:Fuse_1206_3216Metric_Pad1.42x1.75mm_HandSolder | C70076
1k @ 100 MHz | FB1,FB2 | Resistor_SMD:R_0603_1608Metric_Pad0.98x0.95mm_HandSolder
MountingHole_Pad | H1,H2,H3,H4 | MountingHole:MountingHole_3.2mm_M3_Pad
Motor1 | J1,J4 | Connector_PinHeader_2.54mm:PinHeader_1x04_P2.54mm_Horizontal
CAN bus | J10 | Connector_Molex:Molex_SPOX_5267-04A_1x04_P2.50mm_Vertical
GPIO | J11 | Connector_PinHeader_1.27mm:PinHeader_2x05_P1.27mm_Vertical
ENC_SPI | J12 | Connector_PinHeader_1.27mm:PinHeader_2x05_P1.27mm_Vertical
ENC_INC | J13 | Connector_PinHeader_1.27mm:PinHeader_2x05_P1.27mm_Vertical
Termination | J2 | Connector_PinHeader_2.54mm:PinHeader_1x02_P2.54mm_Vertical
CAN bus | J3 | Connector_Molex:Molex_SPOX_5268-04A_1x04_P2.50mm_Horizontal
I2C | J5 | Connector_Molex:Molex_SPOX_5268-04A_1x04_P2.50mm_Horizontal
Power | J6 | TerminalBlock:TerminalBlock_bornier-2_P5.08mm
USB_C_Receptacle_USB2.0 | J7 | Connector_USB:USB_C_Receptacle_XKB_U262-16XN-4BVC11
Conn_01x05_Male | J8 | Connector_Molex:Molex_SPOX_5267-05A_1x05_P2.50mm_Vertical
I2C | J9 | Connector_Molex:Molex_SPOX_5267-04A_1x04_P2.50mm_Vertical
RST | JP1 | Jumper:SolderJumper-2_P1.3mm_Open_RoundedPad1.0x1.5mm
Jumper_2_Open | JP3,JP4 | Jumper:SolderJumper-2_P1.3mm_Open_TrianglePad1.0x1.5mm
NDT2955 | Q1 | Package_TO_SOT_SMD:SOT-223-3_TabPin2 | C194179
0.22 | R1,R2,R3,R5 | Resistor_SMD:R_1206_3216Metric_Pad1.30x1.75mm_HandSolder
1M | R8,R10 | Resistor_SMD:R_0402_1005Metric_Pad0.72x0.64mm_HandSolder
0R | R7,R11 | Resistor_SMD:R_0402_1005Metric_Pad0.72x0.64mm_HandSolder | C17168
47R9 | R12,R13 | Resistor_SMD:R_0603_1608Metric_Pad0.98x0.95mm_HandSolder | C23182
100k | R18 | Resistor_SMD:R_0402_1005Metric_Pad0.72x0.64mm_HandSolder | C25741
4k7 | R19 | Resistor_SMD:R_0402_1005Metric_Pad0.72x0.64mm_HandSolder | C25900
1k | R20,R21,R24 | Resistor_SMD:R_0402_1005Metric_Pad0.72x0.64mm_HandSolder | C25879
5k1 | R22,R23 | Resistor_SMD:R_0402_1005Metric_Pad0.72x0.64mm_HandSolder | C25905
2k2 | R25,R26 | Resistor_SMD:R_0402_1005Metric_Pad0.72x0.64mm_HandSolder | C25879
10k | R4,R9 | Resistor_SMD:R_0402_1005Metric_Pad0.72x0.64mm_HandSolder | C25744
47R | R6 | Resistor_SMD:R_0402_1005Metric_Pad0.72x0.64mm_HandSolder | C23182
BOOT_SW | SW2 | Button_Switch_SMD:SW_SPDT_PCM12
STM32F405RGTx | U1 | Package_QFP:LQFP-64_10x10mm_P0.5mm | C15742
TMC2226-SA | U2,U4 | tmc:TMC2226-SA
MCP2562-E-SN | U3 | Package_SO:SOIC-8_3.9x4.9mm_P1.27mm | C53609
MCP1700-3302E_SOT23 | U6 | Package_TO_SOT_SMD:SOT-23 | C39051
USBLC6-2SC6 | U7 | Package_TO_SOT_SMD:SOT-23-6 | C7519
25 MHz | Y1 | Crystal:Crystal_SMD_3225-4Pin_3.2x2.5mm_HandSoldering | C9006

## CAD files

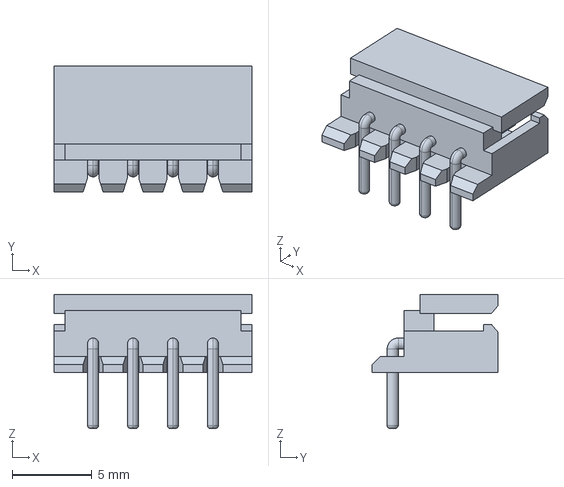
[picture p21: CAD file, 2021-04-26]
Hardware/rev2/molex_04_l.stp
12.4 x 7.90 x 8.40 mm

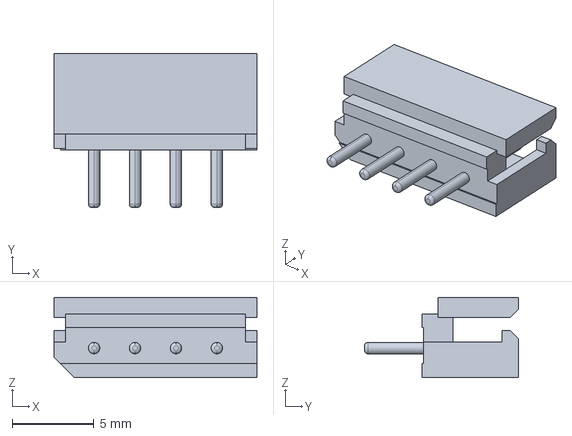
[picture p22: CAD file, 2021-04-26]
Hardware/rev2/molex_04_v.stp
12.4 x 9.40 x 4.90 mm

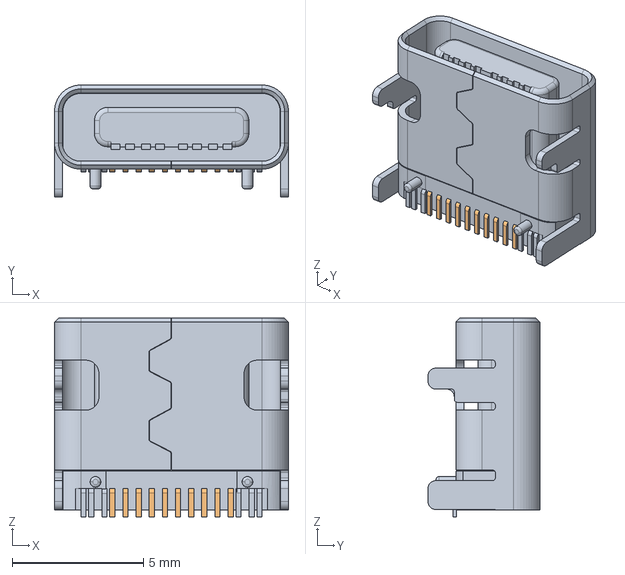
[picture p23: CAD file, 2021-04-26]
Hardware/rev2/u262-16xn-4bvc11.stp
8.90 x 4.26 x 7.56 mm

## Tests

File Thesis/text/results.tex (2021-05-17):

\chapter{Results}
\label{ch:results}
This chapter discusses the implemented functionality, features and the final state of the project in general.
Apart from the final project state, two demonstrations are showcased - one of them being a small mobile robot for indoor mapping, and the second one being a stepper motor driven linear rail useful, for example, for camera movement.

\section{Final Project State}
\label{sec:final_project_state}
This section describes the final state of the SM4 stepper motor controller project.
In the Figures below, we can see both of the manufactured \acs{pcb} revisions.
There were two pieces of each of the \acs{pcb} revisions manufactured.
Furthermore, the \acs{API}s for all of the buses are described.

\begin{figure}[H]
    \begin{minipage}[t]{0.45\textwidth}
        \centering
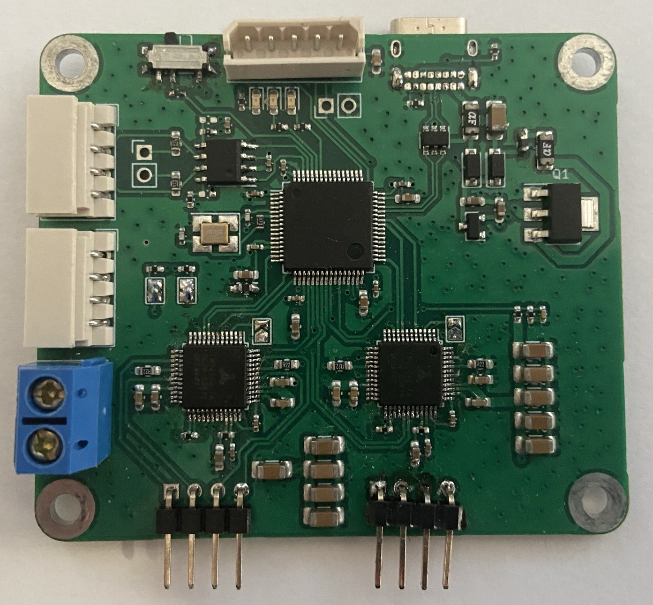
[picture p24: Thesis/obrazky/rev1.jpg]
        
        \caption{The manufactured revision 1 PCB.}
        \label{fig:rev1_pcb}
    \end{minipage}\hfill
    \begin{minipage}[t]{0.45\textwidth}
        \centering
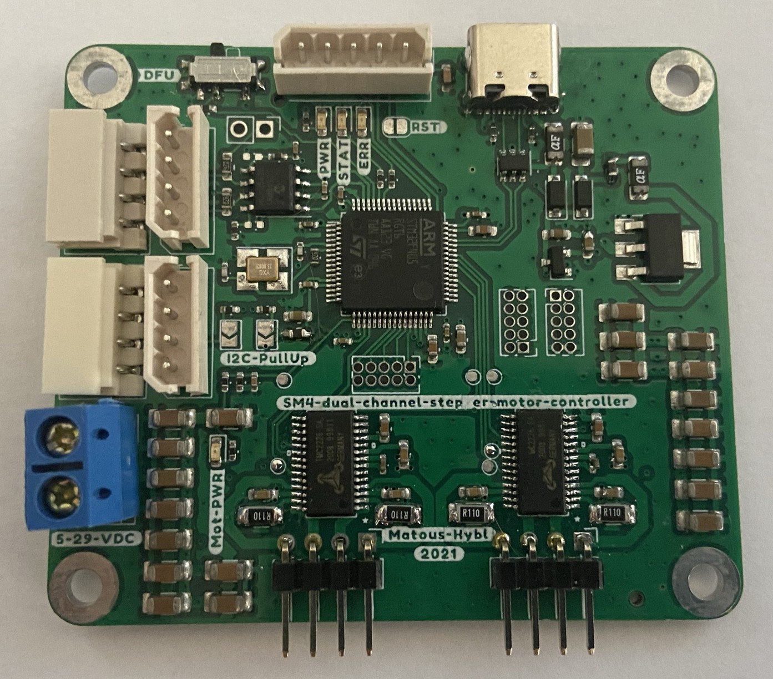
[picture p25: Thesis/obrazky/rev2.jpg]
        
        \caption{The manufactured revision 2 PCB.}
        \label{fig:rev2_pcb}
    \end{minipage}
\end{figure}

In general, two revisions of the hardware have been developed, but only the first one has been used for firmware development due to time constraints.
The majority of the requirements have been fulfilled.
The stepper motor controller is capable of independently driving two stepper motors in either velocity or position mode.
Thanks to the Trinamic driver \acs{ic}s, the motor operation is silent.
The driver now utilizes simulated encoders to measure output shaft position.
Given the controller's design, it can be controlled using the CANOpen protocol or via I\textsuperscript{2}C and can be configured using the USB interface.

\subsection{Requirements Fulfilment}
\label{subsec:req_fulfilment}
At the beginning of the development, we specified requirements in the Section~\ref{sec:requirements}.
The majority of the requirements have been fulfilled, but we will describe the unfulfilled requirements alongside their current fulfilment status in the Table~\ref{tab:unfulfilled_req}.

\begin{table}[H]
    \centering
    \begin{tabular}{ |p{2cm}|p{6cm}|p{6cm}| }
        \hline
        ID & Requirement & Fulfilment status \\
        \hline
        \hline
        FR-02 & When multiple communication interfaces are connected, the system shall prioritize CAN bus, then I2C. USB has the lowest priority. & We haven't been able to find a mechanism for prioritizing, we believe that this requirement might be changed as it should be the integrator's responsibility to choose only one of the communication interfaces. \\
        \hline
        FR-04 & All relevant values (currents, timings, limits, etc.) shall be configurable via USB or CANOpen SDO protocol. & Now, only a subset of the values is configurable. More values (such as the configuration of communication) will be implemented in future revisions. \\
        \hline
        NFR-03 & The controller shall be configurable using a program for personal computers. & The software for personal computers was developed, but the configuration part is missing as of now. \\
        \hline
        NFR-6 & The firmware should utilize software in the loop integration testing for \acs{qa} & Some software in the loop testing has been drafted with the Encoder abstraction, but more of the software in the loop testing will be done in the future.\\
        \hline
        NFR-7 & The firmware shall be properly documented. & Some parts of the firmware are already documented via the inline documentation, but the majority of the other code is not, but it will be done in the future revision. \\
        \hline
    \end{tabular}
    \caption{Unfulfilled requirements}
    \label{tab:unfulfilled_req}
\end{table}

\subsection{CANOpen API}
As we described in the Sections on firmware development (\ref{sec:firmware}) and the one on CANOpen (~\ref{subsec:canopen}), the firmware utilizes the Object Dictionary as the central configuration storage.
From the higher level systems, this Object Dictionary can be accessed via the SDO protocol using indexes and subindexes which are specified in the Table~\ref{tab:object_dictionary} in the Appendix~\ref{ch:canopen_appendices}.

Apart from accessing the Object Dictionary using SDOs, some important control and configuration values have been made accessible via the PDO protocol.
The structure of the PDOs can be seen in the Tables~\ref{tab:rxpdo1}, \ref{tab:txpdo1}, \ref{tab:velocity_pdo}, \ref{tab:position_pdo} in the Appendix~\ref{ch:canopen_appendices}.
For completeness, the description of the PDOs can be found in the Table~\ref{tab:pdo_meaning}.

\begin{table}[H]
    \centering
    \begin{tabular}{ |p{3cm}|p{10cm}| }
        \hline
        Name & Contents \\
        \hline
        \hline
        TxPDO1 & Contains device status - battery voltage and temperature \\
        \hline
        TxPDO2 & Contains actual velocities of both axes \\
        \hline
        TxPDO3 & Contains actual position of axis 1 \\
        \hline
        TxPDO4 & Contains actual position of axis 2 \\
        \hline
        RxPDO1 & Sets axis mode and enables axes \\
        \hline
        RxPDO2 & Sets target velocities for both axes \\
        \hline
        RxPDO3 & Sets target position for axis 1 \\
        \hline
        RxPDO4 & Sets target position for axis 2 \\
        \hline
    \end{tabular}
    \caption{Simplified PDO contents}
    \label{tab:pdo_meaning}
\end{table}

Alongside the SDO and PDO protocols, also the SYNC and NMT protocols have been implemented.
Note that the device must reach the NMT State Operational in order to enable motion control.

\subsection{I\textsuperscript{2}C API}
For the controller to be usable with the BPC-PRP course, we developed a simplified API for the I\textsuperscript{2}C bus.
Using this API, it is only possible to set the axes mode, enable or disable them and then to set control variables and read them.
In the course, the students utilize control in the velocity mode and then acquire the positions of both axes for odometry calculation.
In the previous Sections, we described that in order for motion control to work, the driver needs to reach NMT State Operational.
With the I\textsuperscript{2}C API, this transition is performed automatically when the axes are enabled.

The API can be found in the Table~\ref{tab:i2c_api} and is based on the I\textsuperscript{2}C protocol described in the Figures~\ref{fig:i2c_r} and \ref{fig:i2c_w}.

\begin{table}[H]
    \centering
    \begin{tabular}{ |p{3cm}|p{2cm}|p{2cm}|p{6cm}| }
        \hline
        Address & R/W & Length [B] & Description \\
        \hline
        \hline
        0x10 & R/W & 2 & axis mode and axis enable \\
        \hline
        0x2X & R/W & 4 & set or read axis velocity, where X denotes the axis (1, 2) \\
        \hline
        0x3X & R/W & 8 & set or read axis position, where X denotes the axis (1, 2) \\
        \hline
        0x40 & W & 8 & set velocity for both axes \\
        \hline
        0x50 & R & 16 & read position from both axes \\
        \hline
    \end{tabular}
    \caption{I\textsuperscript{2}C API}
    \label{tab:i2c_api}
\end{table}

\subsection{USB API}
The implemented USB API was designed to only allow for configuring the device as per the requirements.
The protocol is fairly simple.
There are two types of messages - a request and a transfer message, that can be seen in the Figures~\ref{fig:usb_request} and \ref{fig:usb_tansfer}.

When the higher-level device wants to write a value to the Object Dictionary, it simply sends the data transfer message, where the OD KEY contains the index and the subindex.
On the other hand, when the higher-level device wants to read a value from the Object Dictionary, it sends the data request message, and the controller responds with the data transfer message containing the requested value.

\begin{figure}[H]
    \centering
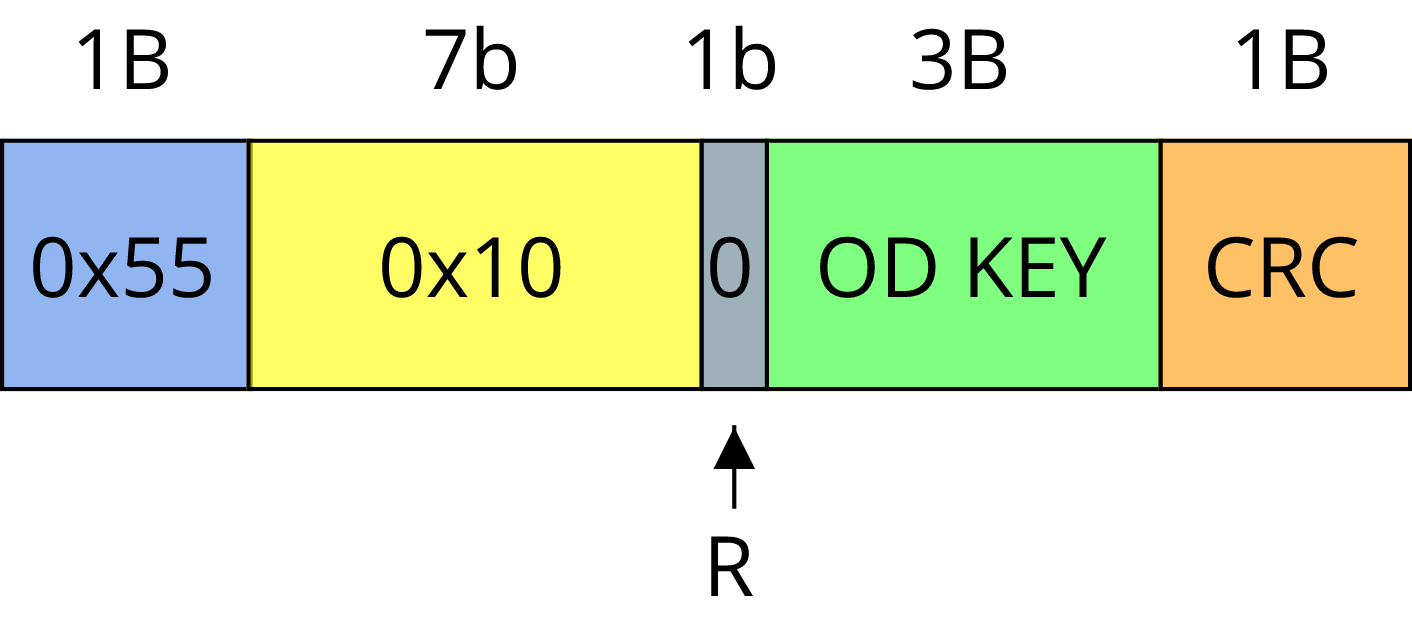
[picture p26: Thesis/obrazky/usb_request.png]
    
    \caption{A data request in the USB API.}
    \label{fig:usb_request}
\end{figure}

\begin{figure}[H]
    \centering
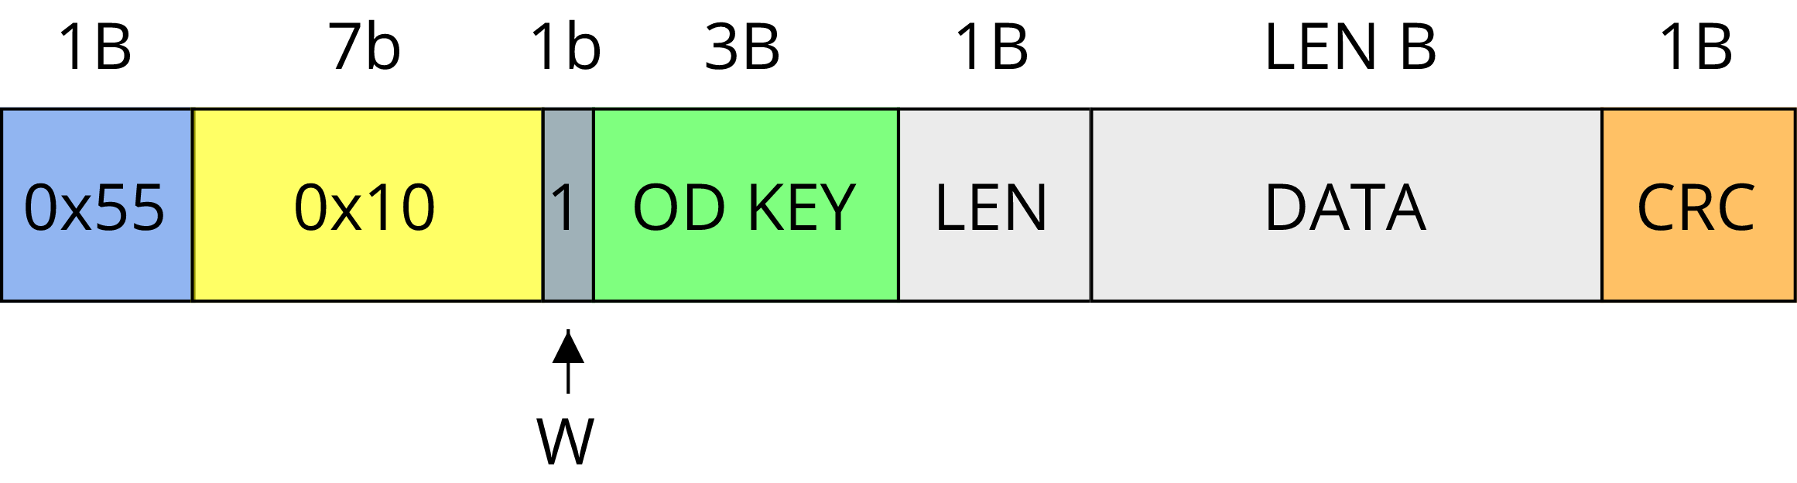
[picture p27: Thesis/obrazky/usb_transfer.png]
    
    \caption{A data transfer in the USB API.}
    \label{fig:usb_tansfer}
\end{figure}

\subsection{Communication Failure Failsafe}
A simple failsafe for the cases when the communication stops was employed.
The failsafe triggers when no control message is received for a specific amount of time.
Therefore it is vital to send the control data periodically.
This is true for both the CANOpen and I\textsuperscript{2}C APIs.

\subsection{Control Application}
A simple control application utilizing the \acs{tui} and CANOpen protocol was developed.
Controlling the stepper motor controller both in velocity and position mode is implemented, but it is not possible to change controller parameters, such as controller constants.
In the future, a fully-featured control application with proper \acs{gui}, support for all the buses and configuration will be developed in order to allow for seamless configuration.
Adding support for flashing via \acs{usb} \acs{dfu} is planned too.

\subsection{Takeaways for Future Revisions}
\label{subsec:final_takeaways}
In this section, we describe what changes we'd made in a possible future revision.
The changes are:
\begin{itemize}
    \item Use the angular XT-30 connector for motor power.
    \item Use different connectors for motors.
    \item Use standardized 10-pin JTAG connector for SWD (Serial Wire Debug).
    \item Use eFuse for electronics protection.
    \item Add more status LEDs.
    \item Improve encoder connector placement, select appropriate connectors.
    \item Remove compatibility resistors around the CAN transceiver.
    \item Attempt to utilize async Rust for easier development.
    \item Rework the schematic to include more information, such as maximal capacitor voltages, add reasoning about component values.
    \item Improve current sensing circuitry to support motors with different phase currents and use sensing resistors with proper power rating. The current should be easily configurable.
    \item Use 4 byte key for object dictionary values.
    \item Properly configure bxCAN filters for CANOpen operation.
\end{itemize}

\section{Demonstration \#1 - Linear Rail Actuator for Camera Movement}
\label{sec:dem2}
The first demonstration for the SM4 motor controller is controlling a single-axis linear rail actuator.
This actuator was provided by the thesis supervisor and is equipped with a NEMA17 style stepper motor that drives a belt with an attached table.
Originally, this rail was meant to be used for camera movement when recording a musician.

This demonstration is controlled using a Raspberry Pi 4B, and the SM4 motor controller is controlled using the I\textsuperscript{2}C bus and the corresponding API.
This showcase aims to demonstrate the controller's ability to control in position mode and, therefore, to position the table on the rail according to the commands of the higher-level system, and also the usability of I\textsuperscript{2}C bus and API.
In the future, this demonstration will be equipped with a second axis allowing for tilting the mounted camera.
The finished demonstrator can be seen in the Figure~\ref{fig:rail_demonstrator}.

\begin{figure}[H]
    \centering
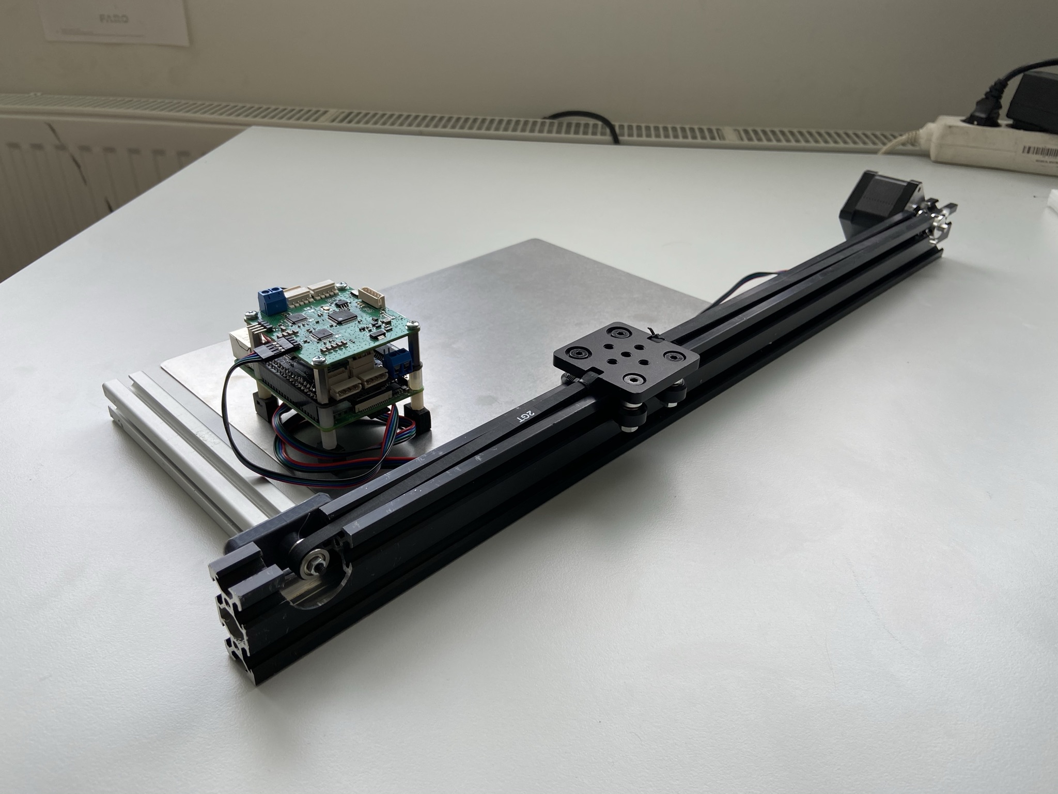
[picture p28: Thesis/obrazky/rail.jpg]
    
    \caption{Linear rail for camera movement - the first demonstration of the SM4 stepper motor controller.}
    \label{fig:rail_demonstrator}
\end{figure}

\section{Demonstration \#2 - Small Mobile Robot for Indoor Mapping}
\label{sec:dem1}
\epigraph{
    Any exploration program which "just happens" to include a new launch vehicle is, de facto, a launch vehicle program. \newline\newline
    (alternate formulation) The three keys to keeping a new human space program affordable and on schedule: \newline
1)  No new launch vehicles. \newline
2)  No new launch vehicles. \newline
3)  Whatever you do, don't develop any new launch vehicles.}{Akin's Laws of Spacecraft Design\cite{akin_akins_nodate}}

The second demonstration, where we showcase the SM4 stepper motor controller, is a small differentially driven robot aimed for indoor mapping and self-localization.
The chassis is differential with a motor on two sides of the robot, which showcases the driver's ability to control both of the motors and calculate odometry.
Apart from the driver itself, the robot features a Raspberry Pi 4B SBC, 4-cell Li-Ion battery, step-down converter, and a simple planar LIDAR for the mapping task.
A block diagram of this demonstration can be seen in the Figure~\ref{fig:mapbot_block}

\begin{figure}[H]
    \centering
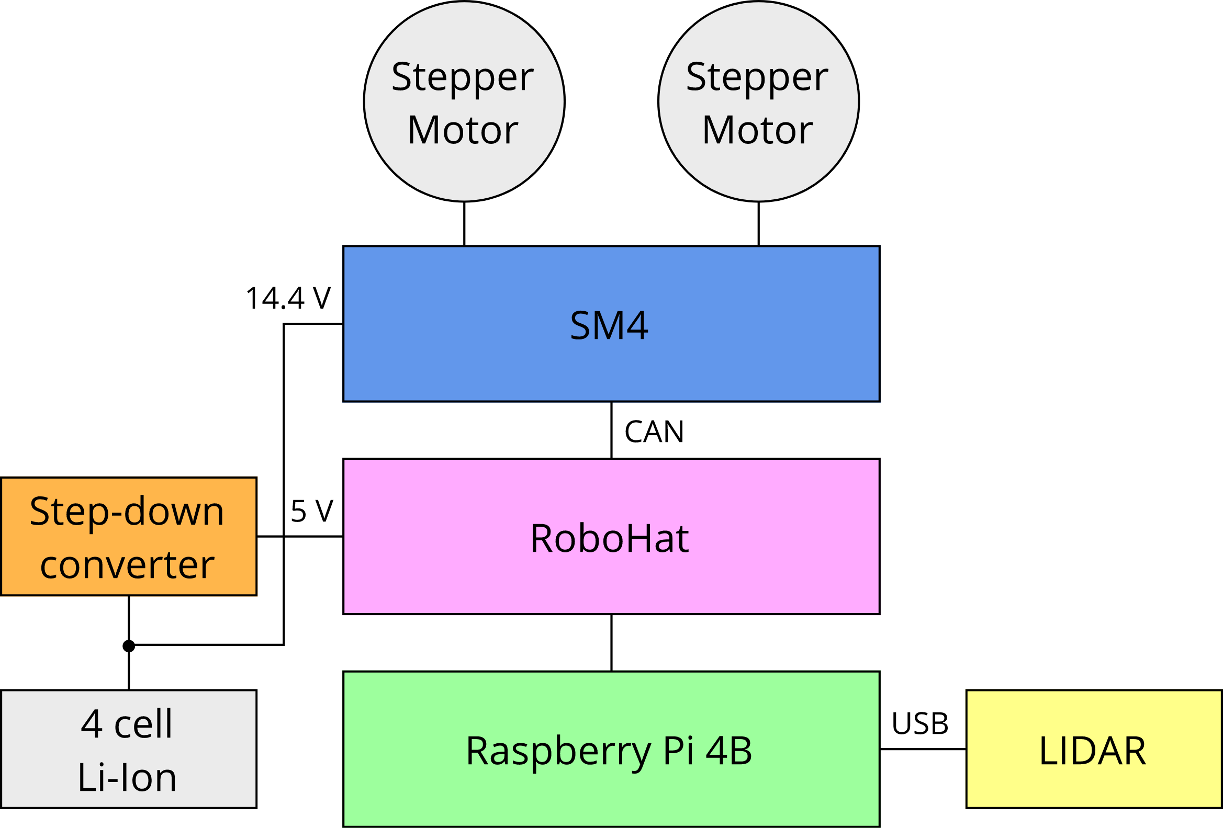
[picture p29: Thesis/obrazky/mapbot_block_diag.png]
    
    \caption{The block diagram of the robot used for the second demonstration.}
    \label{fig:mapbot_block}
\end{figure}

It is projected that the robot will be utilized for algorithm demonstration as part of the MPC-MAP - Advanced Mapping and Self-Localization for Robotics course.
The finalized robot can be seen in the Figure~\ref{fig:map_bot}.

\begin{figure}[H]
    \centering
    
    \caption{The MAP-bot robot - the second demonstration of the SM4 stepper motor controller.}
    \label{fig:map_bot}
\end{figure}

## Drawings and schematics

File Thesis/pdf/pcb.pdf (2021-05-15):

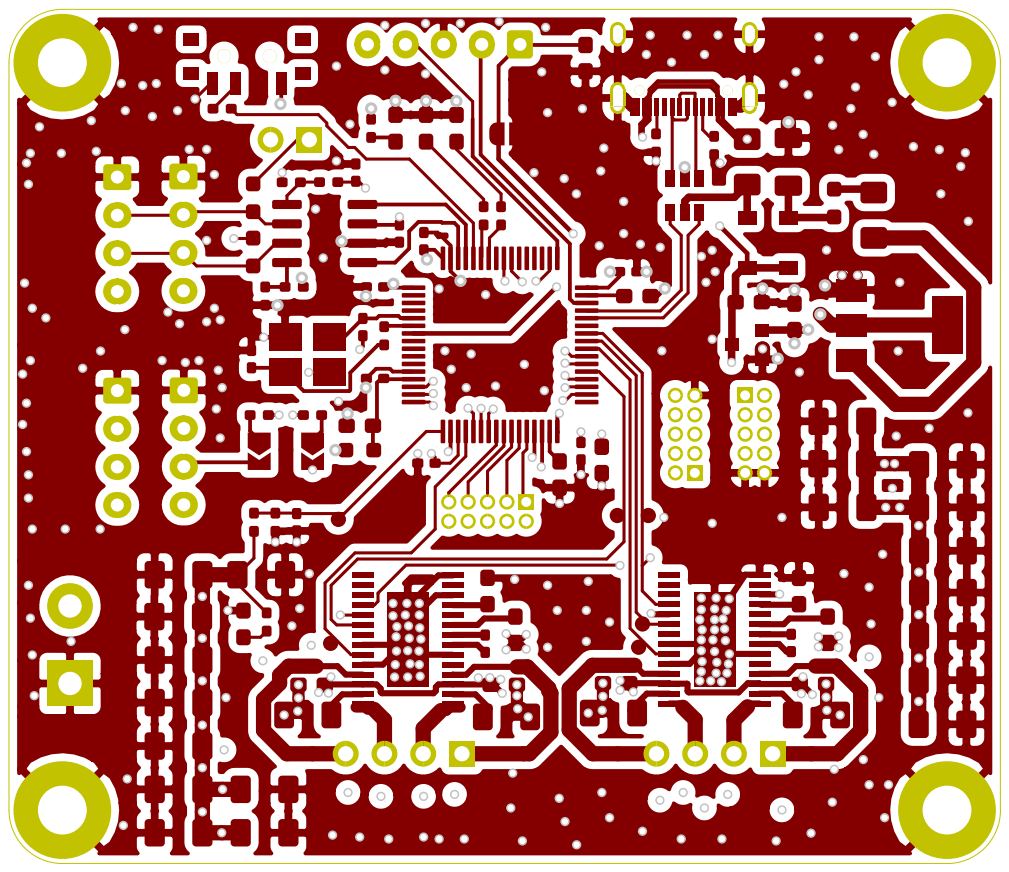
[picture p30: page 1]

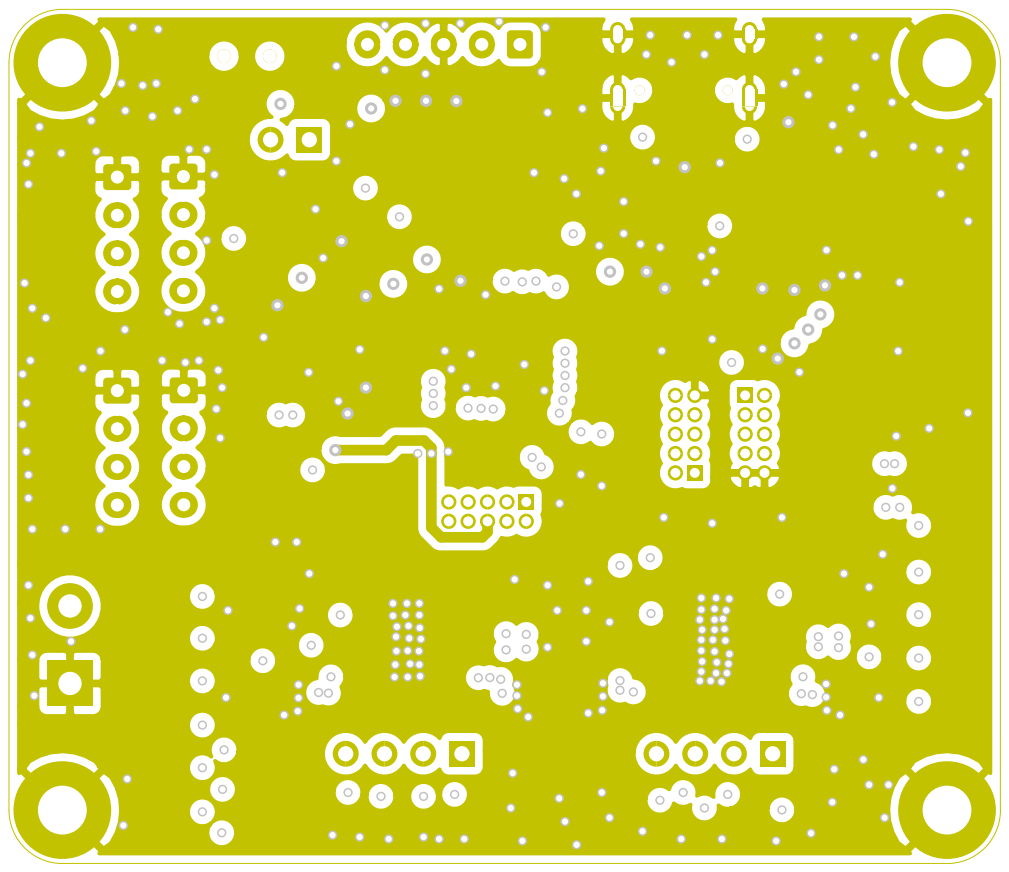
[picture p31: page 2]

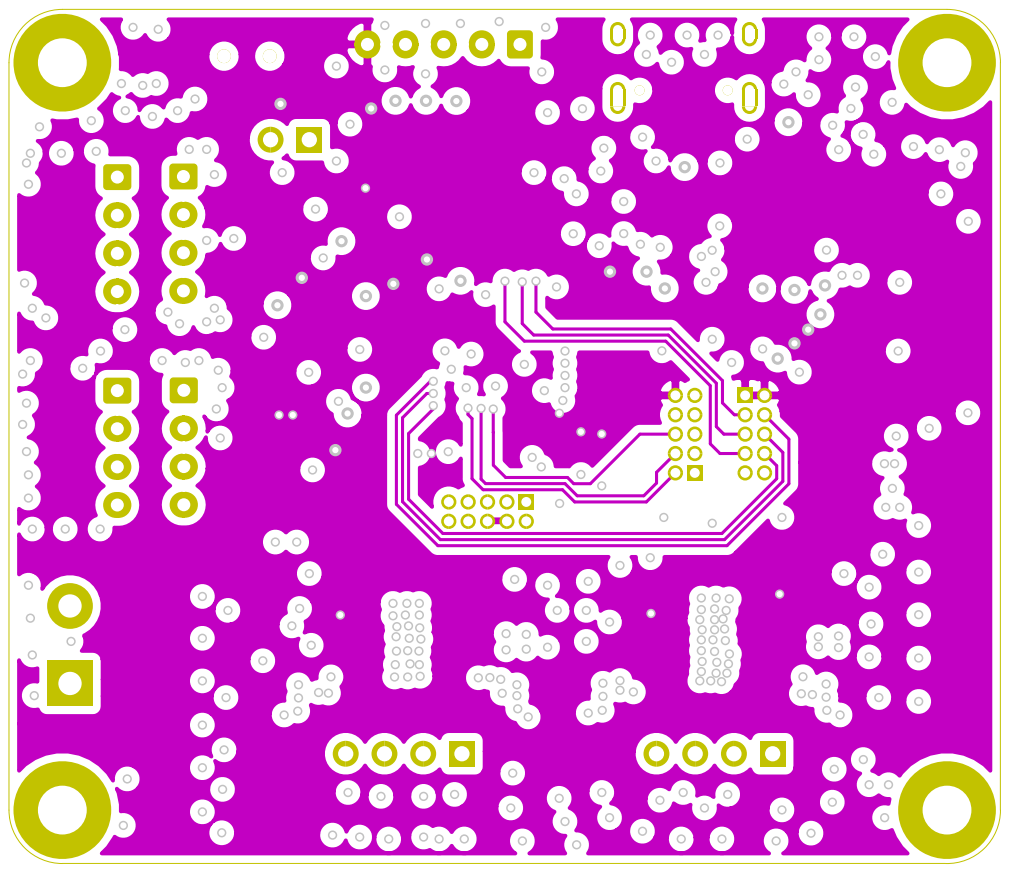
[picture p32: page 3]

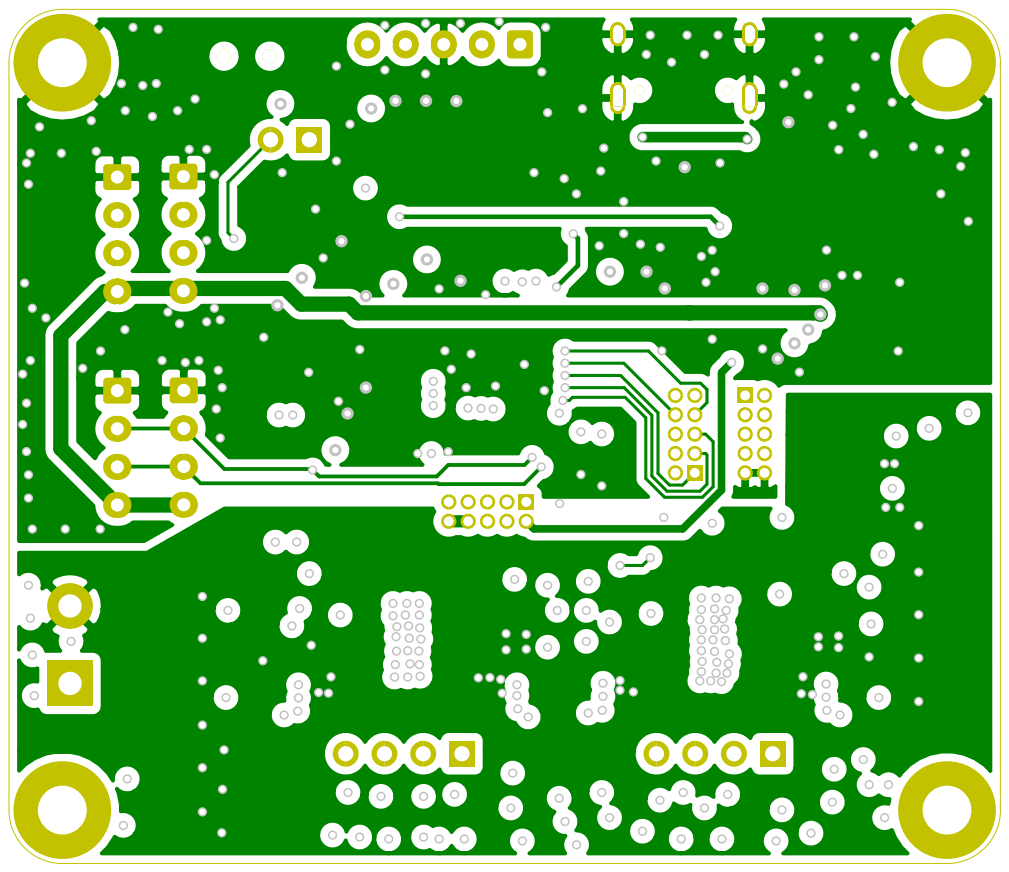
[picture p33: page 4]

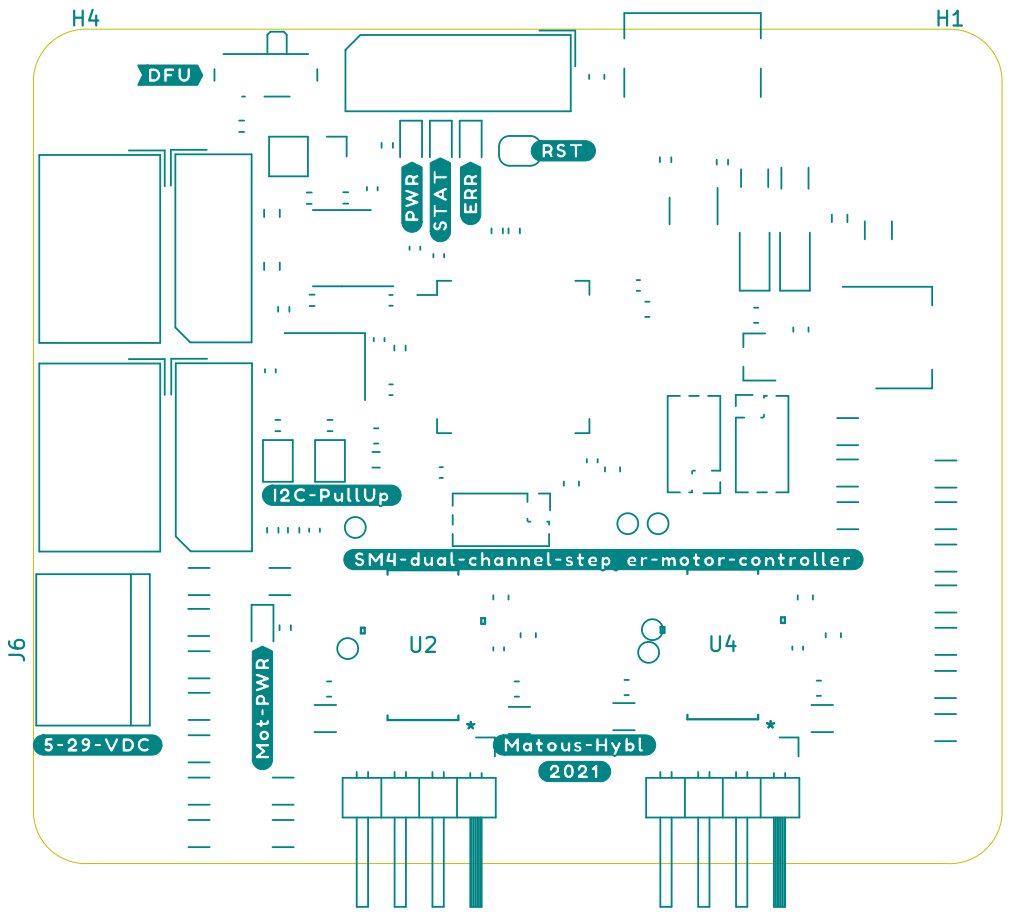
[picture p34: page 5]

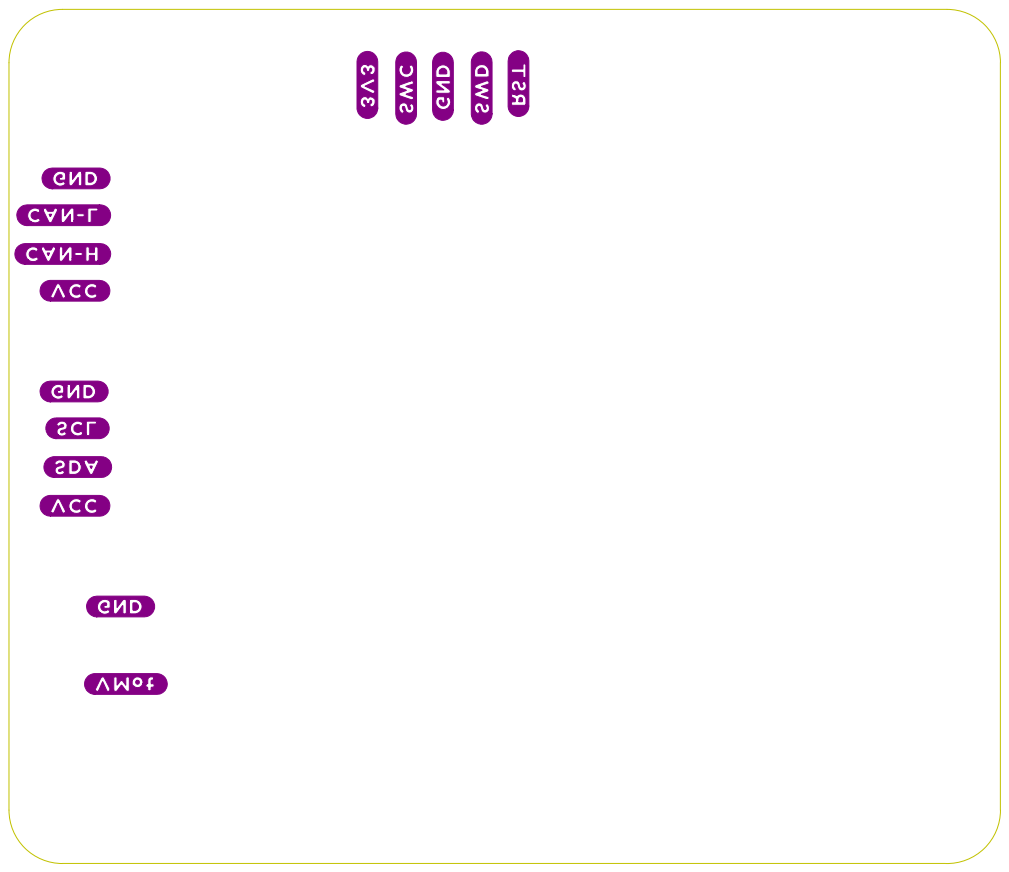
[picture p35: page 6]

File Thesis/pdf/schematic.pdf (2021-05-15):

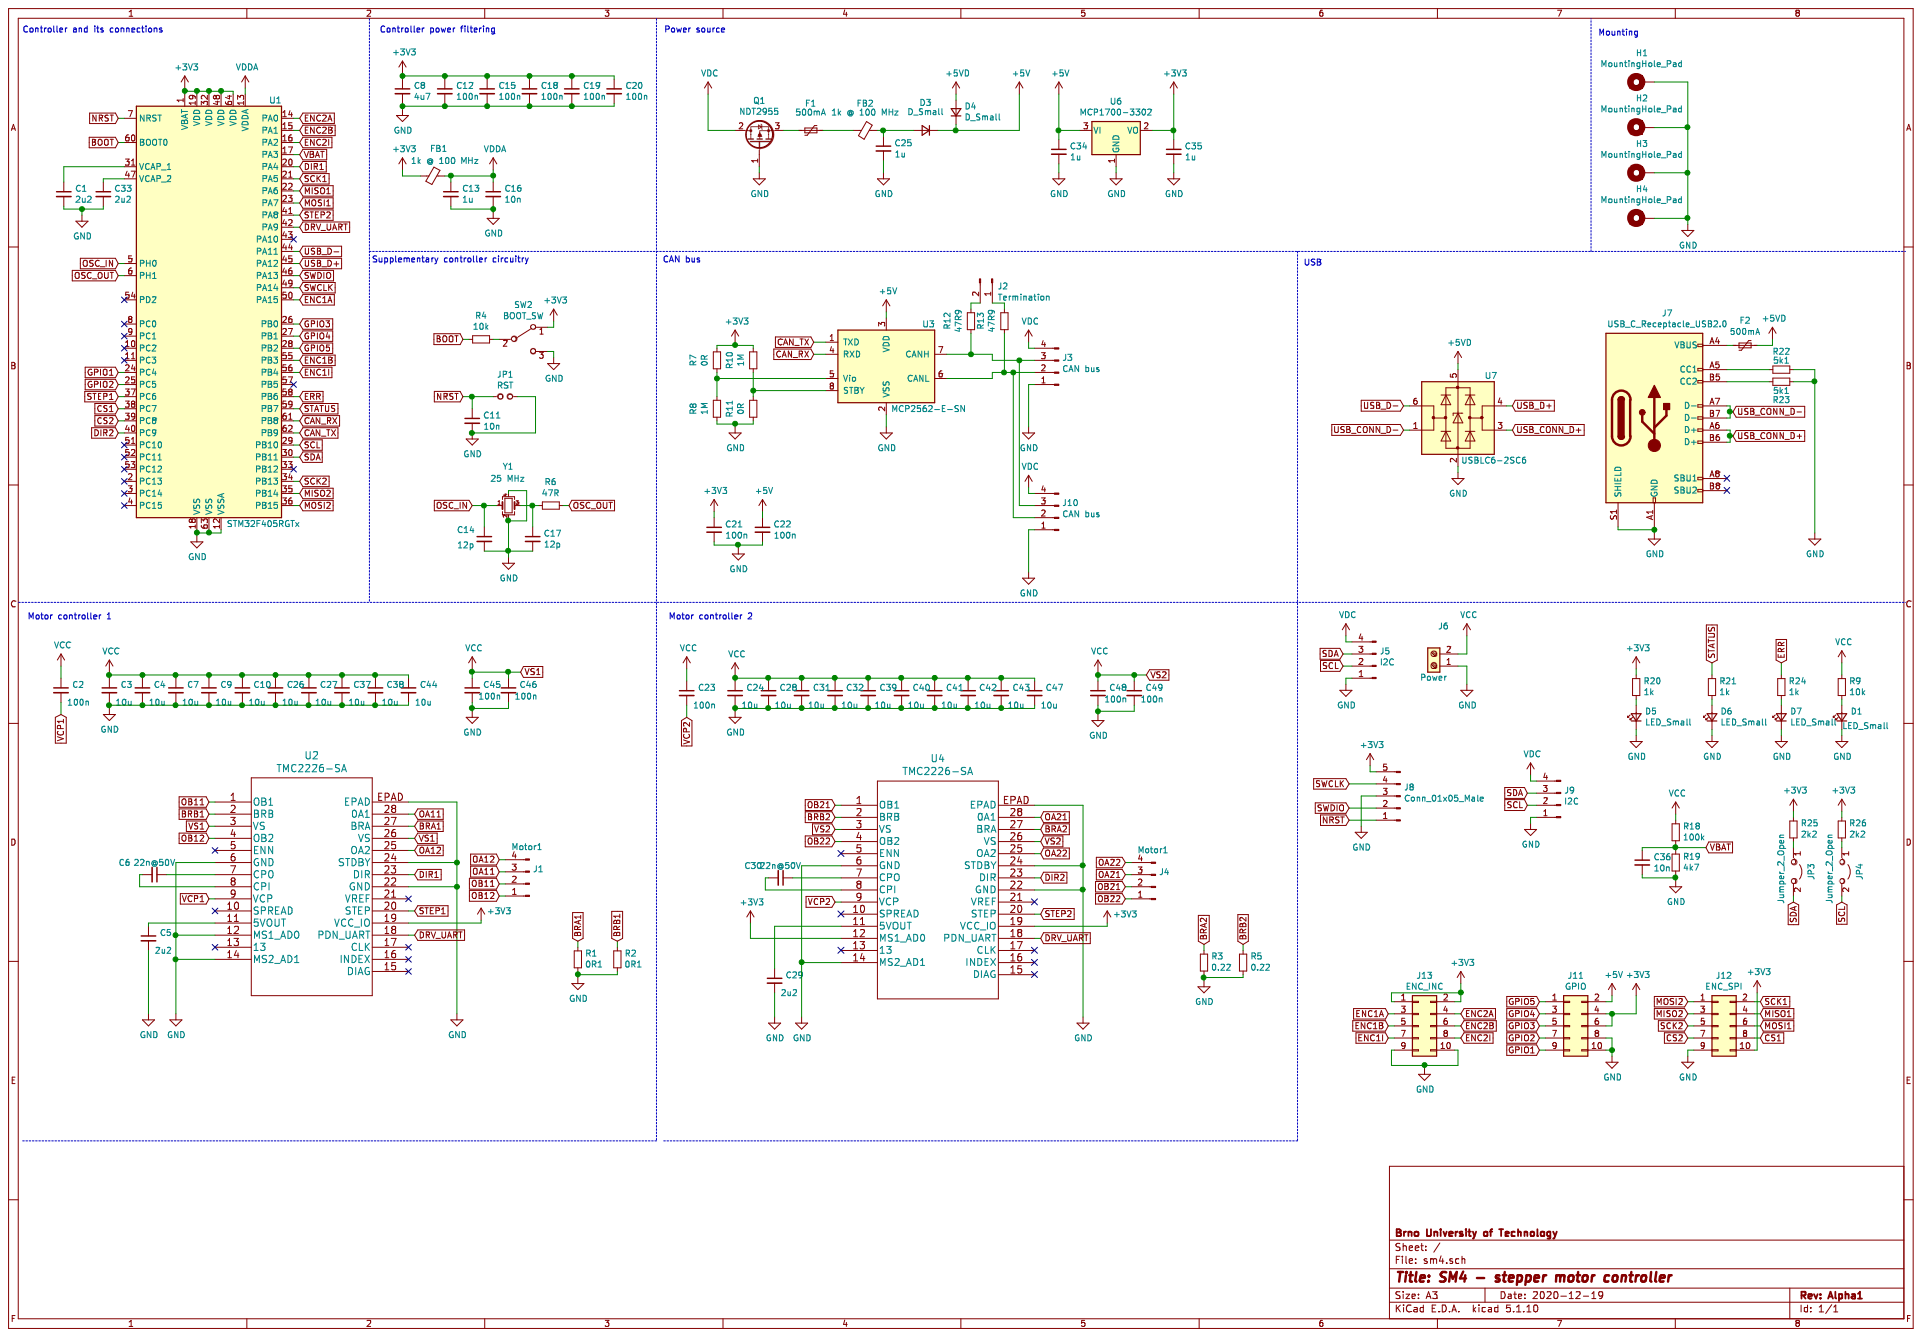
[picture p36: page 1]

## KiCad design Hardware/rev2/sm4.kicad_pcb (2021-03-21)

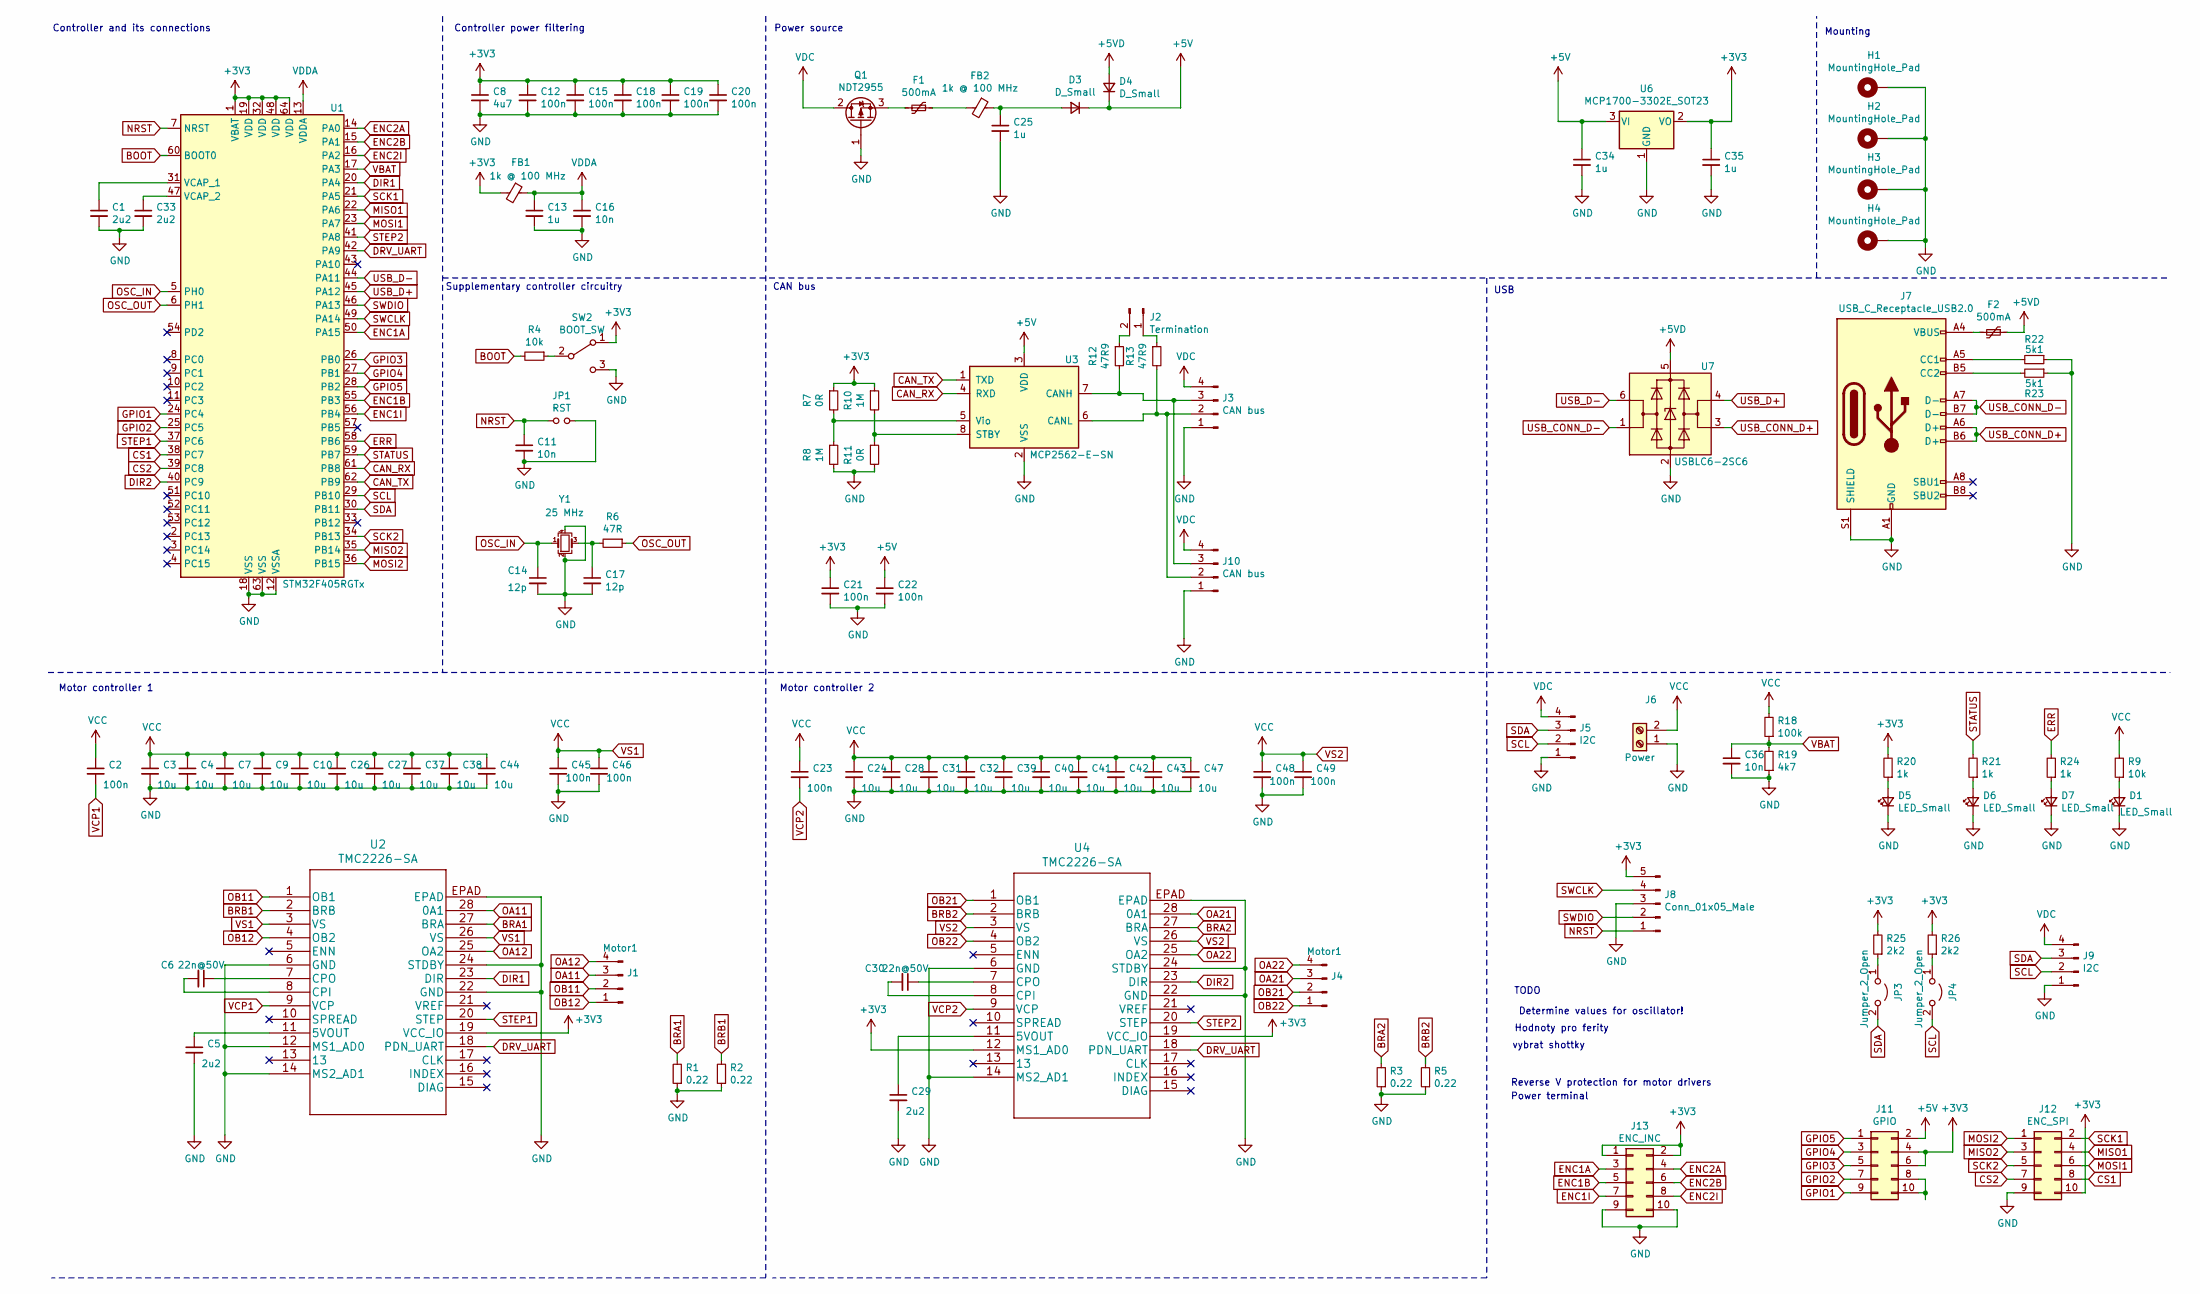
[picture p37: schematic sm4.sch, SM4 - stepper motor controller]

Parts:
C1, C33: 2u2; C_0603_1608Metric_Pad1.08x0.95mm_HandSolder; LCSC C23630
C2, C23, C45, C46, C48, C49: 100n; C_0603_1608Metric_Pad1.08x0.95mm_HandSolder; LCSC C14663
C3, C4, C7, C9, C10, C24, C26, C27, C28, C31, C32, C37, C38, C39, C40, C41, C42, C43, C44, C47: 10u; C_1206_3216Metric_Pad1.33x1.80mm_HandSolder; LCSC C13585
C5, C29: 2u2; C_0603_1608Metric_Pad1.08x0.95mm_HandSolder; LCSC C13585
C6, C30: 22n@50V; C_0402_1005Metric_Pad0.74x0.62mm_HandSolder; LCSC C1532
C8: 4u7; C_0603_1608Metric_Pad1.08x0.95mm_HandSolder; LCSC C19666
C11: 10n; C_0603_1608Metric_Pad1.08x0.95mm_HandSolder; LCSC C57112
C12, C15, C18, C19, C20, C21, C22: 100n; C_0402_1005Metric_Pad0.74x0.62mm_HandSolder; LCSC C1525
C13, C34, C35: 1u; C_0603_1608Metric_Pad1.08x0.95mm_HandSolder; LCSC C15849
C14, C17: 12p; C_0402_1005Metric_Pad0.74x0.62mm_HandSolder; LCSC C1547
C16, C36: 10n; C_0402_1005Metric_Pad0.74x0.62mm_HandSolder; LCSC C15195
C25: 1u; C_1206_3216Metric_Pad1.33x1.80mm_HandSolder; LCSC C1848
D1, D5: LED_Small; LED_0603_1608Metric_Pad1.05x0.95mm_HandSolder; LCSC C72038
D3, D4: D_Small; D_SOD-123; LCSC C8598
D6: LED_Small; LED_0603_1608Metric_Pad1.05x0.95mm_HandSolder; LCSC C72043
D7: LED_Small; LED_0603_1608Metric_Pad1.05x0.95mm_HandSolder; LCSC C2286
F1, F2: 500mA; Fuse_1206_3216Metric_Pad1.42x1.75mm_HandSolder; LCSC C70076
FB1, FB2: 1k @ 100 MHz; R_0603_1608Metric_Pad0.98x0.95mm_HandSolder
H1, H2, H3, H4: MountingHole_Pad; MountingHole_3.2mm_M3_Pad
J1, J4: Motor1; PinHeader_1x04_P2.54mm_Horizontal
J2: Termination; PinHeader_1x02_P2.54mm_Vertical
J3: CAN bus; Molex_SPOX_5268-04A_1x04_P2.50mm_Horizontal
J5: I2C; Molex_SPOX_5268-04A_1x04_P2.50mm_Horizontal
J6: Power; TerminalBlock_bornier-2_P5.08mm
J7: USB_C_Receptacle_USB2.0; USB_C_Receptacle_XKB_U262-16XN-4BVC11
J8: Conn_01x05_Male; Molex_SPOX_5267-05A_1x05_P2.50mm_Vertical
J9: I2C; Molex_SPOX_5267-04A_1x04_P2.50mm_Vertical
J10: CAN bus; Molex_SPOX_5267-04A_1x04_P2.50mm_Vertical
J11: GPIO; PinHeader_2x05_P1.27mm_Vertical
J12: ENC_SPI; PinHeader_2x05_P1.27mm_Vertical
J13: ENC_INC; PinHeader_2x05_P1.27mm_Vertical
JP1: RST; SolderJumper-2_P1.3mm_Open_RoundedPad1.0x1.5mm
JP3, JP4: Jumper_2_Open; SolderJumper-2_P1.3mm_Open_TrianglePad1.0x1.5mm
Q1: NDT2955; SOT-223-3_TabPin2; LCSC C194179
R1, R2, R3, R5: 0.22; R_1206_3216Metric_Pad1.30x1.75mm_HandSolder
R4: 10k; R_0402_1005Metric_Pad0.72x0.64mm_HandSolder; LCSC C25744
R6: 47R; R_0402_1005Metric_Pad0.72x0.64mm_HandSolder; LCSC C23182
R7, R11: 0R; R_0402_1005Metric_Pad0.72x0.64mm_HandSolder; LCSC C17168
R8, R10: 1M; R_0402_1005Metric_Pad0.72x0.64mm_HandSolder
R9: 10k; R_0402_1005Metric_Pad0.72x0.64mm_HandSolder; LCSC C25879
R12, R13: 47R9; R_0603_1608Metric_Pad0.98x0.95mm_HandSolder; LCSC C23182
R18: 100k; R_0402_1005Metric_Pad0.72x0.64mm_HandSolder; LCSC C25741
R19: 4k7; R_0402_1005Metric_Pad0.72x0.64mm_HandSolder; LCSC C25900
R20, R21, R24: 1k; R_0402_1005Metric_Pad0.72x0.64mm_HandSolder; LCSC C25879
R22, R23: 5k1; R_0402_1005Metric_Pad0.72x0.64mm_HandSolder; LCSC C25905
R25, R26: 2k2; R_0402_1005Metric_Pad0.72x0.64mm_HandSolder; LCSC C25879
SW2: BOOT_SW; SW_SPDT_PCM12
U1: STM32F405RGTx; LQFP-64_10x10mm_P0.5mm; LCSC C15742
U2, U4: TMC2226-SA
U3: MCP2562-E-SN; SOIC-8_3.9x4.9mm_P1.27mm; LCSC C53609
U6: MCP1700-3302E_SOT23; SOT-23; LCSC C39051
U7: USBLC6-2SC6; SOT-23-6; LCSC C7519
Y1: 25 MHz; Crystal_SMD_3225-4Pin_3.2x2.5mm_HandSoldering; LCSC C9006

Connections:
+3V3: C8.1, C12.1, C15.1, C18.1, C19.1, C20.1, C21.1, C35.1, FB1.2, J8.5, J11.4, J11.6, J12.10, J13.1, J13.2, R7.1, R10.1, R20.2, R25.2, R26.2, SW2.1 (A), U1.1 (VBAT), U1.19 (VDD), U1.32 (VDD), U1.48 (VDD), U1.64 (VDD), U2.19 (VCC_IO), U4.12 (MS1_AD0), U4.19 (VCC_IO), U6.2 (VO)
+5V: C22.1, C34.1, D3.1 (K), D4.1 (K), J11.2, U3.3 (VDD), U6.3 (VI)
+5VD: D4.2 (A), F2.1, U7.5 (VBUS)
BOOT: R4.2, U1.60 (BOOT0)
BRA1: R1.2, U2.27 (BRA)
BRA2: R3.2, U4.27 (BRA)
BRB1: R2.2, U2.2 (BRB)
BRB2: R5.2, U4.2 (BRB)
CAN_RX: U1.61 (PB8), U3.4 (RXD)
CAN_TX: U1.62 (PB9), U3.1 (TXD)
CS1: J12.8, U1.38 (PC7)
CS2: J12.7, U1.39 (PC8)
DIR1: U1.20 (PA4), U2.23 (DIR)
DIR2: U1.40 (PC9), U4.23 (DIR)
DRV_UART: U1.42 (PA9), U2.18 (PDN_UART), U4.18 (PDN_UART)
ENC1A: J13.3, U1.50 (PA15)
ENC1B: J13.5, U1.55 (PB3)
ENC1I: J13.7, U1.56 (PB4)
ENC2A: J13.4, U1.14 (PA0)
ENC2B: J13.6, U1.15 (PA1)
ENC2I: J13.8, U1.16 (PA2)
ERR: R24.2, U1.58 (PB6)
GND: C1.2, C3.2, C4.2, C5.2, C7.2, C8.2, C9.2, C10.2, C11.2, C12.2, C13.2, C14.2, C15.2, C16.2, C17.2, C18.2, C19.2, C20.2, C21.2, C22.2, C24.2, C25.2, C26.2, C27.2, C28.2, C29.2, C31.2, C32.2, C33.2, C34.2, C35.2, C36.2, C37.2, C38.2, C39.2, C40.2, C41.2, C42.2, C43.2, C44.2, C45.2, C46.2, C47.2, C48.2, C49.2, D1.1 (K), D5.1 (K), D6.1 (K), D7.1 (K), H1.1, H2.1, H3.1, H4.1, J3.1, J5.1, J6.1, J7.A1 (GND), J7.A12 (GND), J7.B1 (GND), J7.B12 (GND), J7.S1 (SHIELD), J8.3, J9.1, J10.1, J12.9, J13.9, J13.10, JP1.2, Q1.1 (G), R1.1, R2.1, R3.1, R5.1, R8.2, R11.2, R19.1, R22.1, R23.1, SW2.3 (C), U1.12 (VSSA), U1.18 (VSS), U1.63 (VSS), U2.6 (GND), U2.12 (MS1_AD0), U2.14 (MS2_AD1), U2.22 (GND), U2.24 (STDBY), U2.EPAD, U3.2 (VSS), U4.6 (GND), U4.14 (MS2_AD1), U4.22 (GND), U4.24 (STDBY), U4.EPAD, U6.1 (GND), U7.2 (GND), Y1.2, Y1.4
GPIO1: J11.9, U1.24 (PC4)
GPIO2: J11.7, U1.25 (PC5)
GPIO3: J11.5, U1.26 (PB0)
GPIO4: J11.3, U1.27 (PB1)
GPIO5: J11.1, U1.28 (PB2)
MISO1: J12.4, U1.22 (PA6)
MISO2: J12.3, U1.35 (PB14)
MOSI1: J12.6, U1.23 (PA7)
MOSI2: J12.1, U1.36 (PB15)
NRST: C11.1, J8.1, JP1.1, U1.7 (NRST)
unnamed: C1.1, U1.31 (VCAP_1)
unnamed: C5.1, U2.11 (5VOUT)
unnamed: C6.1, U2.7 (CPO)
unnamed: C6.2, U2.8 (CPI)
unnamed: C17.1, R6.2, Y1.3
unnamed: C25.1, D3.2 (A), FB2.1
unnamed: C29.1, U4.11 (5VOUT)
unnamed: C30.1, U4.7 (CPO)
unnamed: C30.2, U4.8 (CPI)
unnamed: C33.1, U1.47 (VCAP_2)
unnamed: D1.2 (A), R9.1
unnamed: D5.2 (A), R20.1
unnamed: D6.2 (A), R21.1
unnamed: D7.2 (A), R24.1
unnamed: F1.1, FB2.2
unnamed: F1.2, Q1.3 (S)
unnamed: F2.2, J7.A4 (VBUS), J7.A9 (VBUS), J7.B4 (VBUS), J7.B9 (VBUS)
unnamed: J2.1, R13.1
unnamed: J2.2, R12.1
unnamed: J7.A5 (CC1), R22.2
unnamed: J7.B5 (CC2), R23.2
unnamed: J3.2, J10.2, R13.2, U3.6 (CANL)
unnamed: J3.3, J10.3, R12.2, U3.7 (CANH)
unnamed: J11.8, J11.10
unnamed: JP3.1 (A), R25.1
unnamed: JP4.1 (A), R26.1
unnamed: R4.1, SW2.2 (B)
unnamed: R7.2, R8.1, U3.5 (Vio)
unnamed: R10.2, R11.1, U3.8 (STBY)
OA11: J1.3, U2.28 (0A1)
OA12: J1.4, U2.25 (OA2)
OA21: J4.3, U4.28 (0A1)
OA22: J4.4, U4.25 (OA2)
OB11: J1.2, U2.1 (OB1)
OB12: J1.1, U2.4 (OB2)
OB21: J4.2, U4.1 (OB1)
OB22: J4.1, U4.4 (OB2)
OSC_IN: C14.1, U1.5 (PH0), Y1.1
OSC_OUT: R6.1, U1.6 (PH1)
SCK1: J12.2, U1.21 (PA5)
SCK2: J12.5, U1.34 (PB13)
SCL: J5.2, J9.2, JP4.2 (B), U1.29 (PB10)
SDA: J5.3, J9.3, JP3.2 (B), U1.30 (PB11)
STATUS: R21.2, U1.59 (PB7)
STEP1: U1.37 (PC6), U2.20 (STEP)
STEP2: U1.41 (PA8), U4.20 (STEP)
SWCLK: J8.4, U1.49 (PA14)
SWDIO: J8.2, U1.46 (PA13)
USB_CONN_D+: J7.A6 (D+), J7.B6 (D+), U7.3 (I/O2)
USB_CONN_D-: J7.A7 (D-), J7.B7 (D-), U7.1 (I/O1)
USB_D+: U1.45 (PA12), U7.4 (I/O2)
USB_D-: U1.44 (PA11), U7.6 (I/O1)
VBAT: C36.1, R18.1, R19.2, U1.17 (PA3)
VCP1: C2.2, U2.9 (VCP)
VCP2: C23.2, U4.9 (VCP)
VDC: J3.4, J5.4, J9.4, J10.4, Q1.2 (D)
VDDA: C13.1, C16.1, FB1.1, U1.13 (VDDA)
VS1: C2.1, C3.1, C4.1, C7.1, C9.1, C10.1, C23.1, C24.1, C26.1, C27.1, C28.1, C31.1, C32.1, C37.1, C38.1, C39.1, C40.1, C41.1, C42.1, C43.1, C44.1, C45.1, C46.1, C47.1, C48.1, C49.1, J6.2, R9.2, R18.2, U2.3 (VS), U2.26 (VS), U4.3 (VS), U4.26 (VS)

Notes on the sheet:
Determine values for oscillator!
Controller and its connections
Controller power filtering
Supplementary controller circuitry
Power source
Mounting
TODO
Hodnoty pro ferity
vybrat shottky
Motor controller 1
Motor controller 2
Reverse V protection for motor drivers
CAN bus
USB
Power terminal

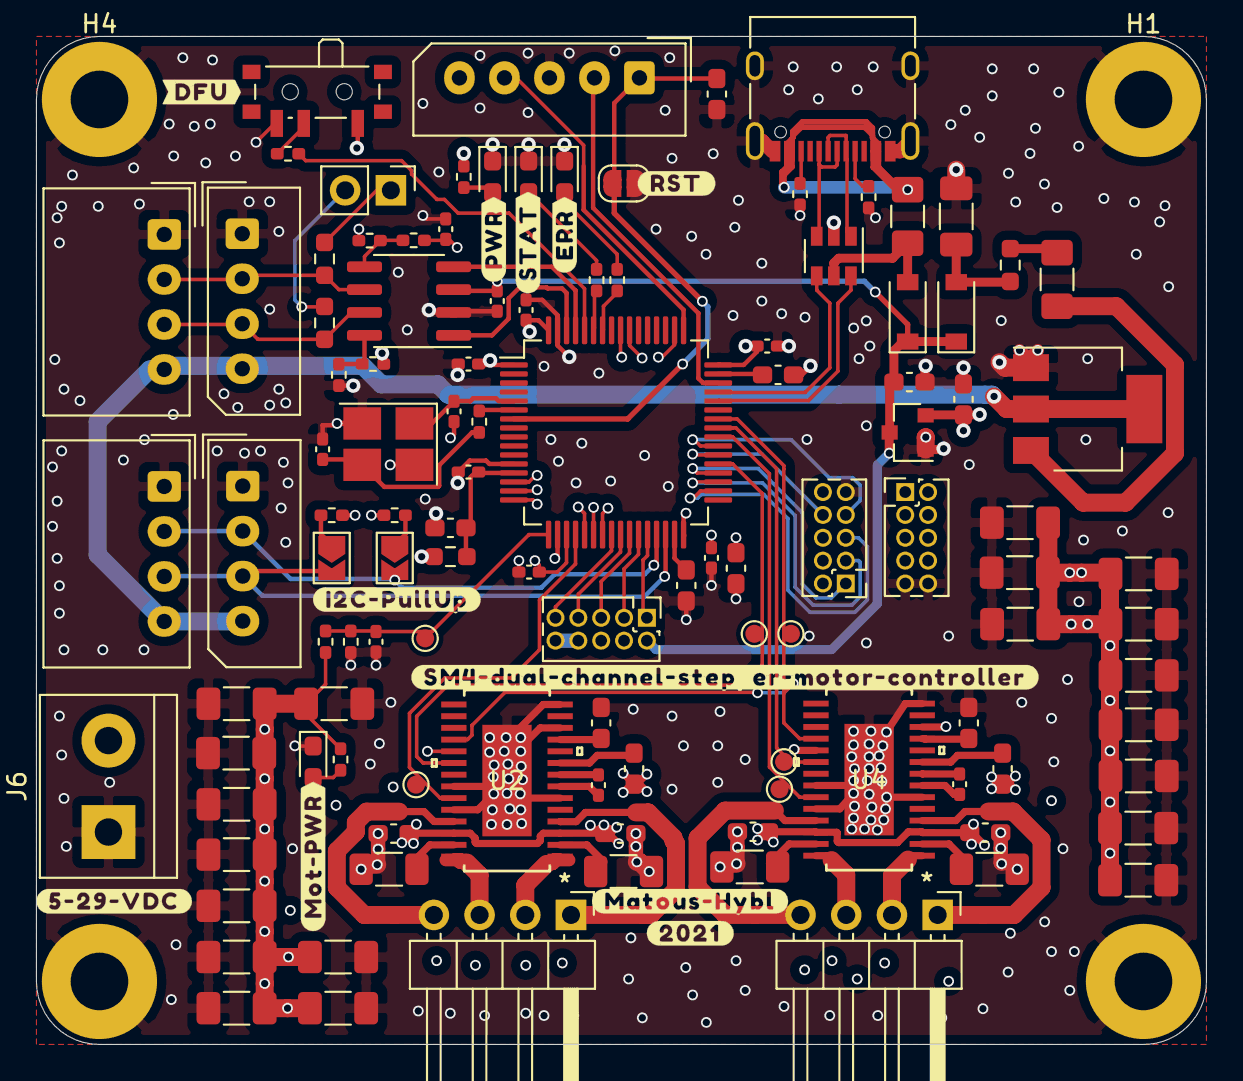
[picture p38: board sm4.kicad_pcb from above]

Board: 4 copper layers, 65.0 x 56.0 mm, 110 parts (0 on the bottom side), 91 nets.

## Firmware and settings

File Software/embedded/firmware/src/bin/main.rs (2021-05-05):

#![no_main]
#![no_std]

use cortex_m::peripheral::DWT;
use rtic::cyccnt::U32Ext as _;
use sm4_firmware as _; // global logger + panicking-behavior + memory layout

use stm32f4xx_hal as hal;

use sm4_firmware::SM4;

#[rtic::app(device = stm32f4xx_hal::stm32, peripherals = true, monotonic = rtic::cyccnt::CYCCNT)]
const APP: () = {
    struct Resources {
        driver: SM4,
    }

    #[init(schedule = [blink, monitoring, control, ramp, failsafe_tick, heartbeat_tick])]
    fn init(cx: init::Context) -> init::LateResources {
        let mut core: rtic::Peripherals = cx.core;
        let device: hal::pac::Peripherals = cx.device;

        core.DCB.enable_trace();
        DWT::unlock();
        core.DWT.enable_cycle_counter();

        let driver = SM4::init(device);

        let now = cx.start;
        cx.schedule
            .blink(now + SM4::blink_period().cycles())
            .unwrap();
        cx.schedule
            .monitoring(now + SM4::monitoring_period().cycles())
            .unwrap();
        cx.schedule
            .control(now + SM4::control_period().cycles())
            .unwrap();
        cx.schedule
            .ramp(now + SM4::ramping_period().cycles())
            .unwrap();
        cx.schedule
            .failsafe_tick(now + SM4::failsafe_tick_period().cycles())
            .unwrap();
        cx.schedule
            .heartbeat_tick(now + SM4::heartbeat_tick_period().cycles())
            .unwrap();

        init::LateResources { driver }
    }

    #[idle(resources = [driver])]
    fn main(_cx: main::Context) -> ! {
        loop {
            cortex_m::asm::nop();
        }
    }

    #[task(binds = OTG_FS, resources = [driver])]
    fn usb_handler(cx: usb_handler::Context) {
        cx.resources.driver.process_usb();
    }

    #[task(resources = [driver], schedule = [blink])]
    fn blink(cx: blink::Context) {
        cx.resources.driver.blink_leds();

        cx.schedule
            .blink(cx.scheduled + SM4::blink_period().cycles())
            .unwrap();
    }

    #[task(resources = [driver], schedule = [monitoring])]
    fn monitoring(cx: monitoring::Context) {
        cx.resources.driver.monitor();

        cx.schedule
            .monitoring(cx.scheduled + SM4::monitoring_period().cycles())
            .unwrap();
    }

    #[task(resources = [driver], schedule = [control])]
    fn control(cx: control::Context) {
        cx.resources.driver.control();

        cx.schedule
            .control(cx.scheduled + SM4::control_period().cycles())
            .unwrap();
    }

    #[task(resources = [driver], schedule = [ramp])]
    fn ramp(cx: ramp::Context) {
        cx.resources.driver.ramp();

        cx.schedule
            .ramp(cx.scheduled + SM4::ramping_period().cycles())
            .unwrap();
    }

    #[task(resources = [driver], schedule = [failsafe_tick])]
    fn failsafe_tick(cx: failsafe_tick::Context) {
        cx.resources.driver.failsafe_tick();

        cx.schedule
            .failsafe_tick(cx.scheduled + SM4::failsafe_tick_period().cycles())
            .unwrap();
    }

    #[task(resources = [driver], schedule = [heartbeat_tick])]
    fn heartbeat_tick(cx: heartbeat_tick::Context) {
        cx.resources.driver.heartbeat_tick();

        cx.schedule
            .heartbeat_tick(cx.scheduled + SM4::heartbeat_tick_period().cycles())
            .unwrap();
    }

    #[task(binds = DMA2_STREAM0, resources = [driver])]
    fn dma(cx: dma::Context) {
        cx.resources.driver.monitoring_complete();
    }

    #[task(binds = CAN1_RX0, resources = [driver])]
    fn can_handler(cx: can_handler::Context) {
        cx.resources.driver.process_can();
    }

    #[task(binds = I2C2_EV, resources = [driver])]
    fn i2c_event_handler(cx: i2c_event_handler::Context) {
        cx.resources.driver.process_i2c_event();
    }

    #[task(binds = I2C2_ER, resources = [driver])]
    fn i2c_error_handler(cx: i2c_error_handler::Context) {
        cx.resources.driver.process_i2c_error();
    }

    extern "C" {
        fn EXTI0();
    }
};

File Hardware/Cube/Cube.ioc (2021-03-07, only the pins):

Mcu.UserName=STM32F405RGTx
PA0-WKUP.GPIO_Label=ENC2A
PA0-WKUP.Signal=S_TIM5_CH1
PA1.GPIO_Label=ENC2B
PA1.Signal=S_TIM5_CH2
PA11.Signal=USB_OTG_FS_DM
PA12.Signal=USB_OTG_FS_DP
PA13.Signal=SYS_JTMS-SWDIO
PA14.Signal=SYS_JTCK-SWCLK
PA15.GPIO_Label=ENC1A
PA15.Signal=S_TIM2_CH1_ETR
PA2.GPIO_Label=ENC2I
PA2.Signal=GPXTI2
PA3.GPIO_Label=VBAT
PA3.Signal=GPIO_Output
PA4.GPIO_Label=DIR1
PA4.Signal=GPIO_Output
PA5.Signal=SPI1_SCK
PA6.Signal=SPI1_MISO
PA7.Signal=SPI1_MOSI
PA8.GPIO_Label=STEP2
PA8.Signal=S_TIM1_CH1
PA9.GPIO_Label=DRV_UART
PA9.Signal=USART1_TX
PB0.GPIO_Label=GPIO3
PB0.Signal=GPIO_Output
PB1.GPIO_Label=GPIO4
PB1.Signal=GPIO_Output
PB10.Signal=I2C2_SCL
PB11.Signal=I2C2_SDA
PB13.Signal=SPI2_SCK
PB14.Signal=SPI2_MISO
PB15.Signal=SPI2_MOSI
PB2.GPIO_Label=GPIO5
PB2.Signal=GPIO_Output
PB3.GPIO_Label=ENC1B
PB3.Signal=S_TIM2_CH2
PB4.GPIO_Label=ENC1I
PB4.Signal=GPXTI4
PB6.GPIO_Label=ERR_LED
PB6.Signal=GPIO_Output
PB7.GPIO_Label=STATUS_LED
PB7.Signal=GPIO_Output
PB8.Signal=CAN1_RX
PB9.Signal=CAN1_TX
PC4.GPIO_Label=GPIO1
PC4.Signal=GPIO_Output
PC5.GPIO_Label=GPIO2
PC5.Signal=GPIO_Output
PC6.GPIO_Label=STEP1
PC6.Signal=S_TIM8_CH1
PC7.GPIO_Label=CS1
PC7.Signal=GPIO_Output
PC8.GPIO_Label=CS2
PC8.Signal=GPIO_Output
PC9.GPIO_Label=DIR2
PC9.Signal=GPIO_Output
PH0-OSC_IN.Signal=RCC_OSC_IN
PH1-OSC_OUT.Signal=RCC_OSC_OUT

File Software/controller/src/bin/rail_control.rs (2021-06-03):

use crossterm::event::KeyCode;
use crossterm::execute;
use crossterm::terminal::{
    disable_raw_mode, enable_raw_mode, EnterAlternateScreen, LeaveAlternateScreen,
};
use i2cdev::core::I2CDevice;
use i2cdev::core::I2CMessage;
use i2cdev::core::I2CTransfer;
use i2cdev::linux::LinuxI2CDevice;
use i2cdev::linux::LinuxI2CError;
use parking_lot::Mutex;
use sm4_controller::canopen_backend::AxisState;
use sm4_controller::canopen_backend::ENCODER_RESOLUTION;
use sm4_controller::tui::SystemEvent;
use sm4_controller::tui::SystemEvents;
use sm4_shared::prelude::Axis;
use sm4_shared::prelude::Position;
use sm4_shared::OnError;
use std::io::Write;
use std::sync::Arc;
use std::time::Duration;
use std::vec;
use tui::{
    backend::{Backend, CrosstermBackend},
    layout::{Constraint, Direction, Layout, Rect},
    style::{Color, Modifier, Style},
    text::{Span, Spans},
    widgets::{Block, Borders, Gauge, Paragraph, Wrap},
    Frame, Terminal,
};

trait I2CRegisterTransfers<Error> {
    fn write_register<R: Into<u8>>(&mut self, register: R, data: &[u8]) -> Result<(), Error>;
    fn read_register<R: Into<u8>>(&mut self, register: R, buffer: &mut [u8]) -> Result<u32, Error>;
}

impl I2CRegisterTransfers<LinuxI2CError> for LinuxI2CDevice {
    fn write_register<R: Into<u8>>(
        &mut self,
        register: R,
        data: &[u8],
    ) -> Result<(), LinuxI2CError> {
        let mut buffer = vec![register.into()];
        buffer.extend_from_slice(data);
        self.write(&buffer)
    }

    fn read_register<R: Into<u8>>(
        &mut self,
        register: R,
        buffer: &mut [u8],
    ) -> Result<u32, LinuxI2CError> {
        self.transfer(&mut [
            I2CMessage::write(&[register.into()]),
            I2CMessage::read(buffer),
        ])
    }
}

#[derive(Clone)]
struct I2CBackend {
    state: Arc<Mutex<AxisState>>,
}

impl I2CBackend {
    fn new(device: LinuxI2CDevice) -> Self {
        let s = Self {
            state: Arc::new(Mutex::new(AxisState::default())),
        };

        std::thread::spawn({
            let s = s.clone();
            let mut device = device;
            device
                .write_register(0x10, &[0x11, 0x0f])
                .on_error(|_| println!("Failed to set driver mode"));
            move || loop {
                let mut data = [0u8; 8];
                {
                    let position = s.state.lock().target_position;
                    data[..4].clone_from_slice(&position.get_revolutions().to_le_bytes());
                    data[4..].clone_from_slice(&position.get_angle().to_le_bytes());
                }
                device
                    .write_register(0x31, &data)
                    .on_error(|_| println!("Failed to write target position."));

                // let mut buffer = [0u8; 16];
                // device
                //     .read_register(0x50, &mut buffer)
                //     .on_error(|_| println!("Failed to read positions."));
                std::thread::sleep(Duration::from_millis(50));
            }
        });

        s
    }

    fn set_target_position(&self, position: Position<ENCODER_RESOLUTION>) {
        self.state.lock().target_position = position;
    }

    fn get_target_position(&self) -> Position<ENCODER_RESOLUTION> {
        self.state.lock().target_position
    }

    fn get_state(&self) -> AxisState {
        *self.state.lock()
    }
}

const MAX_POSITION: Position<ENCODER_RESOLUTION> = Position::<ENCODER_RESOLUTION>::new(10, 0);

fn draw<B: Backend>(state: &AxisState, frame: &mut Frame<B>) {
    let chunks = Layout::default()
        .direction(Direction::Vertical)
        .constraints(
            [
                Constraint::Percentage(20),
                Constraint::Percentage(20),
                Constraint::Percentage(20),
                Constraint::Percentage(35),
                Constraint::Percentage(5),
            ]
            .as_ref(),
        )
        .split(frame.size());
    let gauge = Gauge::default()
        .block(
            Block::default()
                .title(Span::styled(
                    "Position",
                    Style::default()
                        .fg(Color::Magenta)
                        .add_modifier(Modifier::BOLD),
                ))
                .borders(Borders::ALL),
        )
        .gauge_style(Style::default().fg(Color::Yellow))
        .percent(
            (state.actual_position.get_increments() as f32 / MAX_POSITION.get_increments() as f32
                * 100.0) as u16,
        );
    frame.render_widget(gauge, chunks[1]);
    draw_axis_block(state, frame, chunks[3]);
    frame.render_widget(
        Paragraph::new("q - quit, left arrow - move left, right arrow - move right"),
        chunks[4],
    );
}

fn draw_axis_block<B: Backend>(state: &AxisState, frame: &mut Frame<B>, target: Rect) {
    let axis1_data = vec![
        Spans::from(format!("enabled: {}", state.enabled)),
        Spans::from(format!("mode: {}", state.mode())),
        Spans::from(format!("target vel: {}", state.target_velocity)),
        Spans::from(format!("actual vel: {}", state.actual_velocity)),
        Spans::from(format!(
            "target pos: {} - {}",
            state.target_position.get_revolutions(),
            state.target_position.get_angle(),
        )),
        Spans::from(format!(
            "actual pos: {} - {}",
            state.actual_position.get_revolutions(),
            state.actual_position.get_angle(),
        )),
    ];
    let block = Block::default().borders(Borders::ALL).title(Span::styled(
        "Axis parameters",
        Style::default()
            .fg(Color::Magenta)
            .add_modifier(Modifier::BOLD),
    ));
    let paragraph = Paragraph::new(axis1_data)
        .block(block)
        .wrap(Wrap { trim: true });
    frame.render_widget(paragraph, target);
}
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

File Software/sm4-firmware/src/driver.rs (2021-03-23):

use sm4_shared::{
    canopen::NMTState, encoder::Encoder, encoder::Speed, AxisMode, Direction, PSDController,
    StepperDriver,
};

use crate::object_dictionary::ObjectDictionary;
use embedded_time::duration::Microseconds;
use sm4_shared::ramp::TrapRampGen;

const SPEED_COMMAND_RESET_INTERVAL: u8 = 10; // ticks of a failsafe timer

#[derive(Copy, Clone)]
pub struct DriverState {
    nmt_state: NMTState,
    object_dictionary: ObjectDictionary,
    last_received_speed_command_down_counter: u8,
}

impl DriverState {
    pub fn new(encoder_resolution: u16) -> Self {
        let mut s = Self {
            nmt_state: NMTState::default(),
            object_dictionary: ObjectDictionary::new(encoder_resolution),
            last_received_speed_command_down_counter: 0,
        };

        s.object_dictionary
            .set_axis1_target_velocity(Speed::new(1.0));
        s
    }

    pub fn go_to_preoperational_if_needed(&mut self) {
        if self.nmt_state == NMTState::BootUp {
            self.nmt_state = NMTState::PreOperational;
        }
    }

    pub fn go_to_operational(&mut self) {
        self.nmt_state = NMTState::Operational;
    }

    pub fn go_to_stopped(&mut self) {
        self.nmt_state = NMTState::Stopped;
    }

    pub fn go_to_preoperational(&mut self) {
        self.nmt_state = NMTState::PreOperational;
    }

    pub fn is_movement_blocked(&self) -> bool {
        self.nmt_state != NMTState::Operational
            || self.last_received_speed_command_down_counter == 0
    }

    pub fn axis1_target_velocity(&self) -> Speed {
        // if self.is_movement_blocked() || !self.object_dictionary.axis1_enabled() {
        //     Speed::zero()
        // } else {
        self.object_dictionary.axis1_target_velocity()
        // }
    }

    pub fn axis2_target_velocity(&self) -> Speed {
        if self.is_movement_blocked() || !self.object_dictionary.axis2_enabled() {
            Speed::zero()
        } else {
            self.object_dictionary.axis2_target_velocity()
        }
    }

    pub fn decrement_last_received_speed_command_counter(&mut self) {
        if self.last_received_speed_command_down_counter != 0 {
            self.last_received_speed_command_down_counter -= 1;
        }
    }

    pub fn invalidate_last_received_speed_command_counter(&mut self) {
        self.last_received_speed_command_down_counter = SPEED_COMMAND_RESET_INTERVAL;
    }

    pub fn object_dictionary(&mut self) -> &mut ObjectDictionary {
        &mut self.object_dictionary
    }
}

pub struct DualAxisDriver<D1: StepperDriver, D2: StepperDriver, E1: Encoder, E2: Encoder> {
    axis1_driver: D1,
    axis2_driver: D2,
    axis1_encoder: E1,
    axis2_encoder: E2,
    axis1_velocity_controller: PSDController,
    axis2_velocity_controller: PSDController,
    axis1_position_controller: PSDController,
    axis2_position_controller: PSDController,
    axis1_ramp_generator: TrapRampGen,
    axis2_ramp_generator: TrapRampGen,
}

impl<D1: StepperDriver, D2: StepperDriver, E1: Encoder, E2: Encoder>
    DualAxisDriver<D1, D2, E1, E2>
{
    pub fn new(
        axis1_driver: D1,
        axis2_driver: D2,
        axis1_encoder: E1,
        axis2_encoder: E2,
        sampling_period: Microseconds,
    ) -> Self {
        let frequency = 1.0 / (sampling_period.0 as f32 / 1_000_000.0);
        Self {
            axis1_driver,
            axis2_driver,
            axis1_encoder,
            axis2_encoder,
            axis1_velocity_controller: PSDController::new(sampling_period),
            axis2_velocity_controller: PSDController::new(sampling_period),
            axis1_position_controller: PSDController::new(sampling_period),
            axis2_position_controller: PSDController::new(sampling_period),
            axis1_ramp_generator: TrapRampGen::new(frequency),
            axis2_ramp_generator: TrapRampGen::new(frequency),
        }
    }

    pub(crate) fn sample(&mut self, state: &mut DriverState) {
        state.go_to_preoperational_if_needed();
        state.decrement_last_received_speed_command_counter();

        self.axis1_encoder.sample();
        self.axis2_encoder.sample();

        state
            .object_dictionary()
            .set_axis1_actual_velocity(self.axis1_encoder.get_speed());
        state
            .object_dictionary()
            .set_axis2_actual_velocity(self.axis2_encoder.get_speed());

        state
            .object_dictionary()
            .set_axis1_actual_position(self.axis1_encoder.get_position());
        state
            .object_dictionary()
            .set_axis2_actual_position(self.axis2_encoder.get_position());

        // TODO feedback control to object dictionary
        Self::update_axis(
            &mut self.axis1_encoder,
            &mut self.axis1_driver,
            &mut self.axis1_velocity_controller,
            &mut self.axis1_position_controller,
            &mut self.axis1_ramp_generator,
            &state.object_dictionary().axis1_mode(),
            &state.object_dictionary().axis1_target_velocity(),
            &state.object_dictionary().axis1_actual_velocity(),
            &state.object_dictionary().axis1_velocity_p(),
            &state.object_dictionary().axis1_velocity_s(),
            &state.object_dictionary().axis1_velocity_d(),
            &state.object_dictionary().axis1_acceleration(),
            state
                .object_dictionary()
                .axis1_velocity_feedback_control_enable(),
        );

        Self::update_axis(
            &mut self.axis2_encoder,
            &mut self.axis2_driver,
            &mut self.axis2_velocity_controller,
            &mut self.axis2_position_controller,
            &mut self.axis2_ramp_generator,
            &state.object_dictionary().axis2_mode(),
            &state.object_dictionary().axis2_target_velocity(),
            &state.object_dictionary().axis2_actual_velocity(),
            &state.object_dictionary().axis2_velocity_p(),
            &state.object_dictionary().axis2_velocity_s(),
            &state.object_dictionary().axis2_velocity_d(),
            &state.object_dictionary().axis2_acceleration(),
            state
                .object_dictionary()
                .axis2_velocity_feedback_control_enable(),
        );
    }

    // TODO add current manipulation
    // TODO add position control
    pub fn update_axis(
        encoder: &mut dyn Encoder,
        driver: &mut dyn StepperDriver,
        velocity_controller: &mut PSDController,
        position_controller: &mut PSDController,
        ramp_generator: &mut TrapRampGen,
        mode: &AxisMode,
        target_velocity: &Speed,
        actual_velocity: &Speed,
        p: &f32,
        s: &f32,
        d: &f32,
        acceleration: &f32,
        velocity_feedback_control_enabled: bool,
    ) {
        let target_velocity = match mode {
            AxisMode::Velocity => *target_velocity,
            AxisMode::Position => Speed::zero(),
        };
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

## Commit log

2020-12-16 Initial commit.
    [sm4.kicad_pcb, sm4.sch]
2020-12-19 Start working on the schematic.
    [sm4.kicad_pcb, sm4.sch]
2020-12-25 Bring up the firmware project, try timer chaining for odometry reading.
2020-12-29 Add circuitry for the motor controllers.
    [sm4.sch]
2020-12-31 Add packages to components.
    [sm4.kicad_pcb, sm4.sch]
2021-01-04 Finish first version of the PCB, which is trash and shall perish.
    [sm4.kicad_pcb, sm4.sch]
2021-01-07 Implement more of the second version of the PCB.
    [sm4.kicad_pcb, sm4.sch]
2021-01-29 Finalize first HW version. Update firmware project.
    [sm4.kicad_pcb, sm4.sch]
2021-01-30 Implement basic driver, start working on temperature and voltage monitoring.
2021-01-31 Finish temperature and voltage monitoring.
2021-02-07 Fix fmt, add information to debug docs.
    [main.rs]
2021-02-17 Start improving the CANBus implementation.
2021-02-18 Add correct current setting.
    [lib.rs]
2021-02-25 Add failsafe timer, start implementing CANOpen.
    [lib.rs, main.rs]
2021-02-28 Prepare second hardware revision.
    [sm4-B_Cu.gbr, sm4-B_Mask.gbr, sm4-B_Paste.gbr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]
2021-03-03 Start improving the second rev with feedback.
    [sm4.kicad_pcb, sm4.sch]
2021-03-07 Make some final touches to the rev2 hardware.
    [sm4.kicad_pcb, sm4.sch]
2021-03-08 Implement more of the encoder model. Make some final adjustments to rev2 board and order it.
    [sm4.csv, sm4.kicad_pcb, sm4.sch]
2021-03-10 Improve encoder API, start writing tests for it.
2021-03-11 Improve encoder API, start writing tests for it. #2
2021-03-11 Make final adjustments to the encoder abstraction.
2021-03-14 Start implementing simulated encoder, fix some warnings.
    [encoder.rs, lib.rs, step_counter.rs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]
2021-03-15 Fix copypasta in Direction's opposite method.
    [lib.rs]
2021-03-21 Change LED colors. Start working on object dictionary and specify PDO API.
    [sm4.kicad_pcb]
2021-03-22 Move code around, start implementing driver that is independent on the hardware.
2021-03-22 Implement velocity control.
2021-03-23 UNTESTED: implement reception of PDOs and NMT commands. Fix some clippy problems and failing tests.
    [driver.rs, encoder.rs, lib.rs]
2021-04-19 Write some more.
    [sm4.sch]
2021-04-25 Add first TUI controller. Fix bugs in firmware found when testing the TUI controller.
    [canopen_backend.rs, lib.rs, main.rs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]
2021-04-26 Start properly implementing NMT. Add untested current changing.
2021-04-26 Add forgotten dependencies, make position_control work.
    [molex_04_l.stp, molex_04_v.stp, u262-16xn-4bvc11.stp]
2021-04-27 Start refactoring positions, use upstream hal. Fix motion controller.
    [encoder.rs, main.rs, motion_controller.rs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]
2021-04-27 Use const-generics for encoder resolution.
2021-04-27 Copy I2C from KM3. Remove some TODOs.
2021-04-30 Add some text on steppers, update bibliography.
2021-04-30 Write some more text on stepper motors.
2021-05-01 Describe stepper control modes. Start working on driver ICs comparison.
2021-05-02 Finish the section on steppers.
2021-05-05 Add preliminary I2C support (buggy). Fix problem with blocking call on CANOpen.
    [i2c.rs, main.rs, sm4.rs]
2021-05-09 Start working on the text on electronics design.
    [sm4.sch]
2021-05-10 Finish the section on electronics design.
    [sm4.sch]
2021-05-11 Describe software stepper driver and monitoring.
2021-05-11 Describe simulated encoders.
2021-05-14 Document I2C and CANOpen.
2021-05-26 Start working on I2C backend.
2021-06-03 Fix some bugs, add more material to the slideshow.
    [i2c.rs, rail_control.rs, sm4.rs]

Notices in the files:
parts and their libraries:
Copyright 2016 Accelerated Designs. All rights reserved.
